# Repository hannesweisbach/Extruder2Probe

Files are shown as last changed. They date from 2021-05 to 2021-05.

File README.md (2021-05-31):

# Extruder2Probe
Board in stepstick formfactor to attach a PINDA v2 Probe to an empty extruder port

This is part of the modifications of my Sapphire Pro. I wanted to connect a PINDA v2 Z-probe (with temperature sensor). The Sapphire Pro is controlled by an MKS Robin Nano board. 

## Why?
The board has a BLTouch connector, which I could have used, where it not for two issues:

1. my board runs on 3.3V, so it does not have 5V readily available, which the PINDA v2 needs and
2. the BLTouch connector does not connect the temperature sensor of the probe.

## How?

I do, however, use only one extruder, which means the socket for the E1 stepper driver board is empty. This means I have:

* a 4-pin connector for the probe (5V, GND, Signal, Temperature)
* 24V at the stepstick board to generate 5V for the probe
* space to invert the probe signal
* space to condition the analog signal.

The STEP pin on the socket is connected to pin PA6 of the STM23F103 SoC, the DIR pin to pin PA1. PA1 can also be an analog input, hence the temperature sensor has to be connected to this pin.

## Details?

The `EDA` subdirectory contains schematic and board layout in KiCAD format, as well as a [PDF version of the schematic](https://github.com/hannesweisbach/Extruder2Probe/raw/main/EDA/Probe%20Connector.pdf).

Q1 can either be a BJT or MOSFET. R5 is required if Q1 is a BJT, but optional if Q1 is a FET. D2 in conjunction with R5 keeps the gate voltage of Q1 within 0-5V and also acts as a (rudimentary) ESD protection.

## Pictures?

3D rendering of the board:

E2P

Board mounted on the MKS Robin Nano:



With probe attached:



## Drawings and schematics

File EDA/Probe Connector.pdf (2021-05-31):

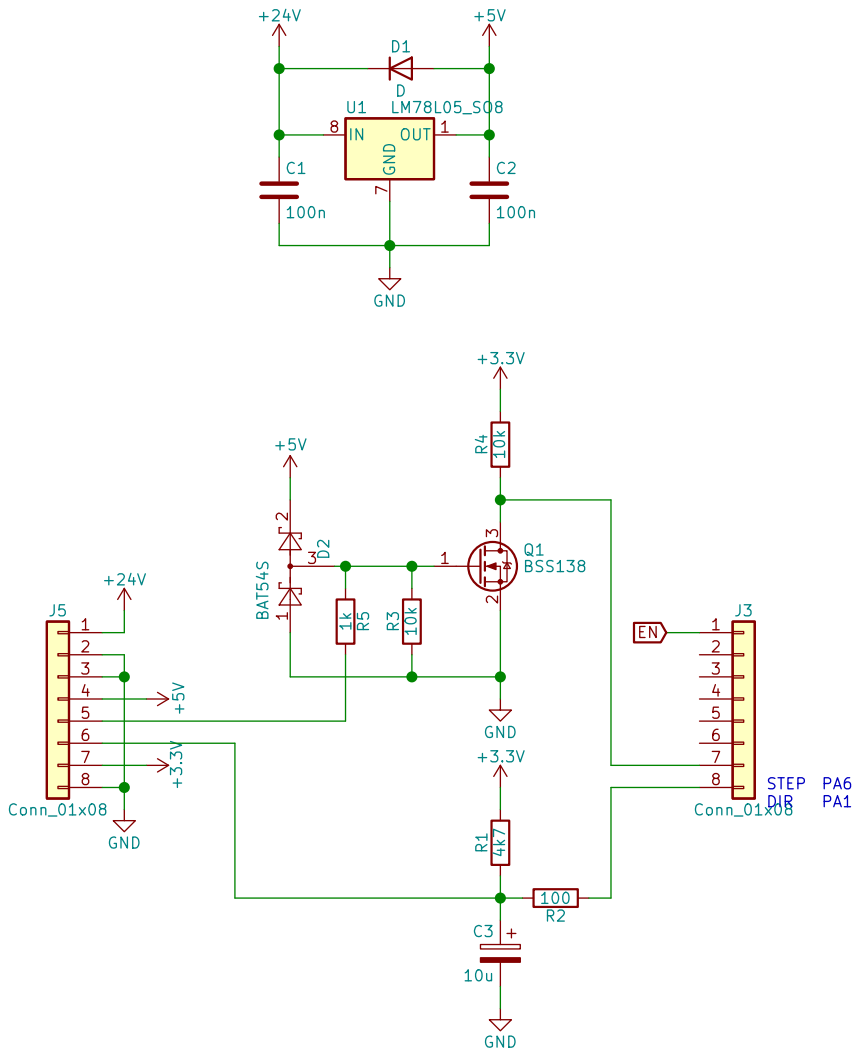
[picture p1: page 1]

Id: 1/1 Title: File: Probe Connector.sch Sheet: /

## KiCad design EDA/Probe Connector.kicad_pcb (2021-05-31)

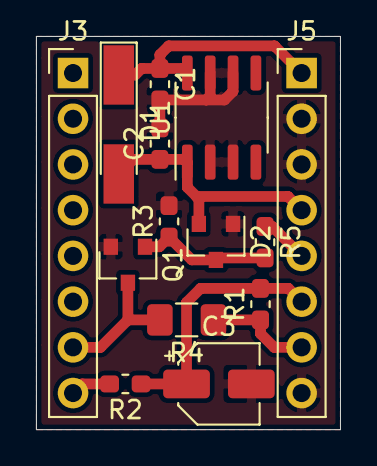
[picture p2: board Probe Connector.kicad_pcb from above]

Board: 2 copper layers, 16.9 x 21.8 mm, 14 parts (0 on the bottom side), 9 nets.

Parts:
C1, C2: 100n; C_0603_1608Metric_Pad1.05x0.95mm_HandSolder
C3: 10u; CP_Elec_4x5.7
D1: D; D_MiniMELF_Handsoldering
D2: BAT54S; SOT-23
J3, J5: Conn_01x08; PinHeader_1x08_P2.54mm_Vertical
Q1: BSS138; SOT-23
R1: 4k7; R_0603_1608Metric_Pad1.05x0.95mm_HandSolder
R2: 100; R_0603_1608Metric_Pad1.05x0.95mm_HandSolder
R3: 10k; R_0603_1608Metric_Pad1.05x0.95mm_HandSolder
R4: 10k; R_1206_3216Metric_Pad1.42x1.75mm_HandSolder
R5: 1k; R_0603_1608Metric_Pad1.05x0.95mm_HandSolder
U1: LM78L05_SO8; SOIC-8_3.9x4.9mm_P1.27mm

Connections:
+3V3: J5.7, R1.1, R4.1
+5V: C2.1, D1.2, D2.2, J5.4, U1.1
+24V: C1.1, D1.1, J5.1, U1.8
GND: C1.2, C2.2, C3.2, D2.1, J5.2, J5.3, J5.8, Q1.2, R3.2, U1.2, U1.3, U1.6, U1.7
unnamed: C3.1, R1.2, R2.1
unnamed: D2.3, Q1.1, R3.1, R5.2
unnamed: J3.7, Q1.3, R4.2
unnamed: J3.8, R2.2
unnamed: J5.5, R5.1

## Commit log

2021-05-31 Add EDA files
    [Probe Connector.kicad_pcb, Probe Connector.sch]
2021-05-31 Add Schematic PDF
2021-05-31 Add link to schematic PDF
2021-05-31 Add explanation of schematic and structure
